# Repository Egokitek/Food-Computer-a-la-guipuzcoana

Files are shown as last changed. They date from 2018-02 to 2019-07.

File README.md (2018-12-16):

# Food-Computer-a-la-guipuzcoana

## Cultivo de alimentos frescos en espacios reducidos mediante un Food Computer

**Proyecto de crowdfunding con** el apoyo de la **Fundación Goteo**, la **Diputación Foral de Gipuzkoa** y [**48 Patrocinadores**](Cofinanciadores.md). La campaña de captación de fondos comenzó el 14 de Septiembre de 2017 y finalizó el 2 de Diciembre del mismo año, habiendo cumplido el objetivo de financiación. EL proyecto se desarrollará durante el año 2018.

 ## Características principales:

**El Food Computer** es la solución ideal para el **cultivo en espacios reducidos en zonas urbanas**, aprovechando cualquier rincón. Es un proyecto de **hardware abierto**, un mini-invernadero con un control muy intenso de las condiciones de cultivo de tal forma que se puede garantizar el clima adecuado. Se pueden cultivar alimentos frescos de km 0. Durante todo el año, fácilmente y con unas tasas de crecimiento muy altas.

**El sistema es escalable**, de tal forma que Food computer tiene 1m3 pero se pueden hacer equipos mas grandes. El consumo de energía es bajo y es posible obtenerlo por vía renovable. Y todo ello con información abierta y disponible para todas en Internet.

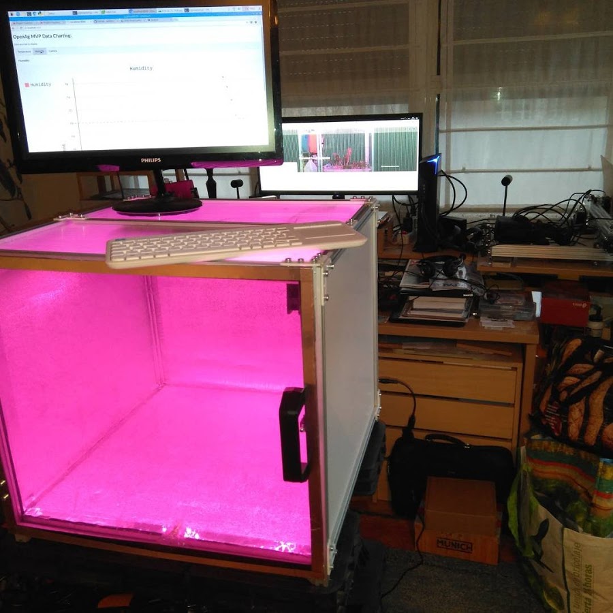
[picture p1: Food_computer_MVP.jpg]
Food Computer MVP


De ese modo se puede cultivar incluso en tierras contaminadas radiactivamente, de hecho el concepto surgió tras una visita a Fukushima de profesorado del MIT. El concepto Food Computer permite conectar vía Internet a otros equipos similares en el mundo, es una especie de red social de agricultores que podrán compartir los parámetros de cultivo o **recetas climáticas** y así conseguir mejorar las cosechas de forma cooperativa y distribuida.

Le quiero añadir funcionalidades que permitan el empleo de biofertilizantes y microorganismos, extracto de agua de mar, etc. Son nutrientes que se pueden crear de forma local y a bajo coste para sustituir a los nutrientes sintéticos que se usan habitualmente en cultivo hidropónico sin tierra. De este modo tendremos un "sustrato vivo" similar al de las tierras mas fértiles y de forma muy asequible y limpia. Integraré también el cultivo de alga spirulina (con una tasa muy elevada de proteínas, calificada de "superalimento").

## Objetivos y recompensas:

Como parte de las recompensas se incluye una unidad de bajo coste y de funciones básicas para comenzar a experimentar, pero el objetivo es construir una unidad completa con todas las funciones y añadir todo lo que se ha comentado. Con ese objetivo cumplido la idea es construir una unidad mas grande de unos 2x2x1m que multiplica las posibilidades. Todo el desarrollo quedará publicado aquí en Github.

## Contenidos de las carpetas:

[**Introducción** ](Introduccion.md) 

Conceptos e Historia del proyecto. Posibilidades que ofrece.

[**Construcción del bastidor** ](Construccion%20bastidor/README.md) 

Varias técnicas constructivas para hacer un bastidor de Food Computer de forma modular, con varios tamaños a elegir.

[**Placa de control - Brain**](Placa%20de%20control%20-%20Brain/README.md) 

Electrónica necesaria para manejar el equipo.

[**Software**](Software/README.md) 

Se utiliza en principio el software **MVP (Minimum Viable Product)**, mas sencillo de implementar y utilizar que el original. 

[**Cultivo**](Cultivo/README.md) 

Metodologías de cultivo.

[**Documentos** ](DOCs/README.md) 

Documentos en formato PDF sobre cultivos de diverso tipo, incluyendo el hidropónico.

[**STLs** ](STL/README.md) 

Ficheros STL listos para imprimir. Necesarios para el desarrollo del proyecto.

[**Varios**](Varios/README.md) 

Diferentes cuestiones que no encajan en el resto de apartados.

## Lista de componentes y presupuesto

El **BOM (Bill of Materials)** está en formato de hoja de calculo excel y tiene varias pestañas que incluye los distintos bastidores realizados y sus diferencias de precio.

En este momento solo está completada la pestaña del FC MVP de 50x50x50 con TSLOT. Próximamente se completará el resto.

El fichero lo tienes [aquí](BOM.xlsx):

## Autor

[**Victor Barahona**](https://github.com/Egokitek)

[**www.egokitek.com**](http://www.egokitek.com)

## Cofinanciadores

[Ver listado **aquí:**](Cofinanciadores.md)

## Créditos

**Food Computer** es un concepto creado por **Caleb Harper** en el **[MIT](http://web.mit.edu/)**, departamento de agricultura abierta **[OpenAg](https://www-prod.media.mit.edu/groups/open-agriculture-openag/overview/)**.

Gran parte de este proyecto está basado en el concepto **[Food Computer MVP](https://forum.openag.media.mit.edu/t/300-food-computer/2343)** (minimum viable product), desarrollado por los miembros de la comunidad OpenAg:
- Peter Webb
- Howard Webb
- Drew Thomas

## Licencia

**GPL3.0**

## En desarrollo actual

- Experimentar y documentar las distintas técnicas de cultivo ya en uso.
- Verificar consumos eléctricos y ver la posibilidad de optimizarlos.
- Probar extracto de agua de mar, biofertilizantes, microorganismos y otros aportes nutricionales.

## Desarrollo futuro

- Integración de cultivo de alga **spirulina**.
- Integración de módulo de **vermicompostaje**.
- Integración de módulo de **acuaponía**.
- Posibilidad de escalado del sistema.

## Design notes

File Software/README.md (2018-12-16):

# Software

### Version MVP

Es la que se ha desarrollado en este proyecto y es la que está utilizando la mayoría de la comunidad. **Ha sido desarrollada por Howard & Peter Webb y Drew Thomas.**

Emplea solo un Raspberry Pi3 sin Arduino, con una tarjeta de 4 relés. Corre sobre un sistema **Linux Raspbian (versión Jessie o Strech)**, a la que se ha añadido los scripts en Python que manejan el equipo.

Desde **Crontab** se controlan las tareas de captura de imágenes, encendido y apagado de luces etc. El sistema contiene un software llamado **Couchdb** que permite almacenar los datos capturados y mantenerlos formateados para verse desde un navegador web.

Desde el navegador **Chromium** (equivalente al Chrome) podemos acceder a los datos mediante un interfaz gráfico. En la foto que sigue vemos su aspecto:

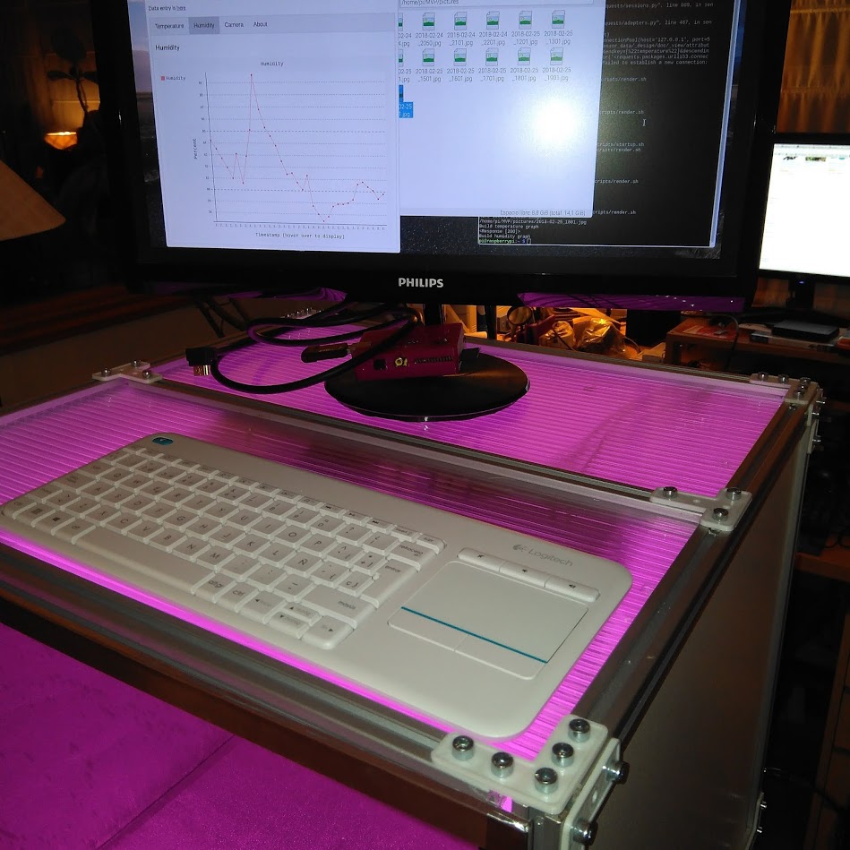
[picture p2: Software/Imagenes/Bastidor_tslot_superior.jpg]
Interfaz gráfico


Tenemos a la izquierda el navegador con la gráfica de humedad seleccionada. A la derecha una carpeta con una serie de fotos capturadas en timelapse del interior.

**Para facilitar la instalación del software**, desde la comunidad se preparó una imagen de la instalación, si se quema directamente a una SD tendremos el software ya instalado y solo tendremos que modificarlo a nivel de variables de entorno. Como esta imagen pesa cerca de 4Gb no se puede incluir aquí.

Para ver el proceso de instalación paso a paso lo veremos mas abajo.

Una vez de tener **una SD configurada podemos clonarla** mediante una aplicación que tiene el sistema Jessie o Strech, de ese modo ahorraremos bastante tiempo en el proceso. Tal y como vemos en esta foto:

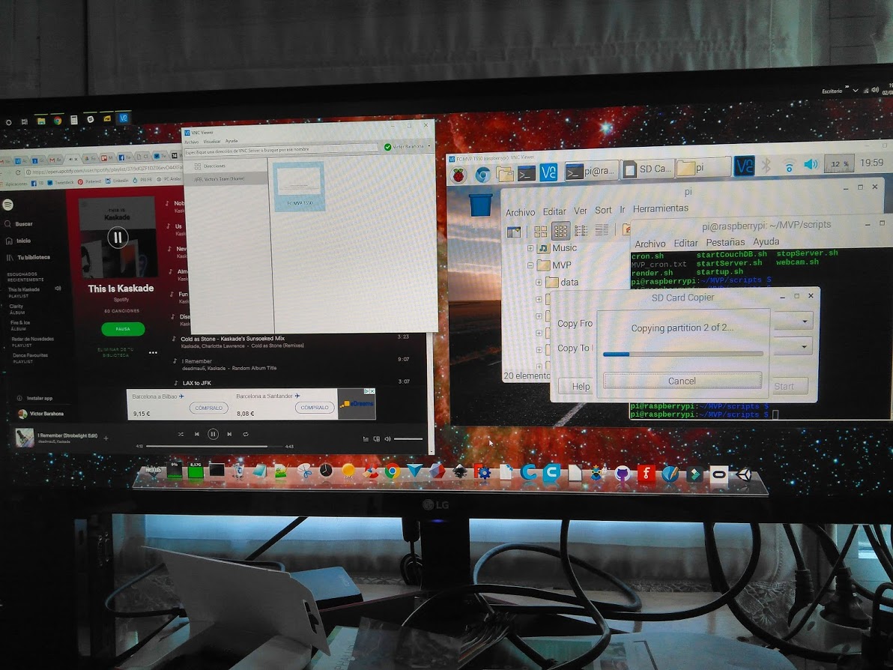
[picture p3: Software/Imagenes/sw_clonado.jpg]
Clonado de software


Una vez de instalado el equipo podemos manejarlo mediante teclado y monitor localmente, o bien habilitar en el Raspberry el **VNC Server** (un SW que lleva incluido por defecto) y **de esa manera podemos operar sobre el de forma remota** desde cualquier lugar. Tal y como vemos aquí:

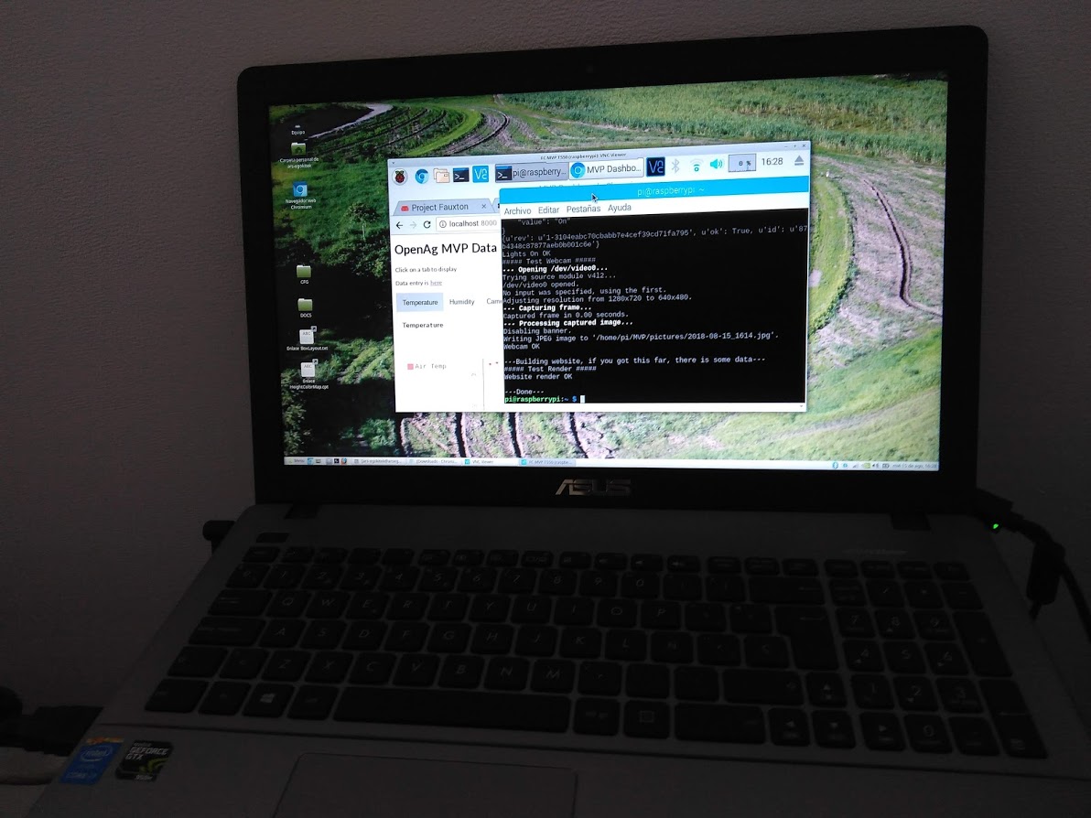
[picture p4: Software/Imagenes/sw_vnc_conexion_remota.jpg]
VNC


Desde el equipo remoto debemos usar el  software VNC viewer. Para ello debemos abrir una cuenta gratuita que nos permitira conectar desde 3 equipos diferentes a 5 unidades. Yo uso mi móvil, el ordenador que tengo en el taller y el ordenador que tengo en la oficina de mi casa. Y puedo conectar a 5 MVPs. Para mas conexiones ya entramos en el plan de pago. Existen alternativas que estoy estudiando.

La comunidad está trabajando también en algún tipo de UI (Interfaz de usuario) que permite operar en varios equipos de forma remota. Se están valorando aplicaciones IoT como NodeRed, Blynk etc. En mi caso sigo utilizando VNC pero si hago algun avance interesante lo publicaré aquí.

### Instalación paso a paso del software

[**En inglés**](Instalation_FC_MVP_ENG.md) Versión original desarrollada por **Howard Webb**

[**En español**](Instalacion_FC_MVP_ESP.md) Versión traducida al castellano  por **Victor Barahona**

La versión en español incluirá modificaciones para utilizar un tercer relé de bombeo de agua y nutrientes. Está en desarrollo y pruebas.

### Comentarios sobre las versiones V1 y V2 del FC

**Las versiones originales del FC V1 y V2** usaban un **Raspberry Pi3, un Arduino y una placa de hasta 16 relés** para controlar los actuadores. Además del software de Arduino la placa Raspberry llevaba su propio software con scripts en JSON y Python. 

Algunos de los problemas que han llevado al abandono de esta línea de trabajo en MArzo de 2018 es la interconectividad de todo este software, problemas con las lecturas de sensores que tenían diferentes tipos de conectores y tensiones de trabajo.

También se comprobaron problemas con la estabilidad del Raspberry Pi debido a que no tiene propiamente un disco duro sino una tarjeta SD que contiene el sistema. Las sucesivas operaciones de lectura/escritura en la misma provocaban una corrupción de datos. Si esta se producía en algún fichero crítico del sistema éste se quedaba "colgado".

### Comentarios sobre la versión V3 EDU

**La nueva V3 EDU** lanzada en Noviembre de 2018 utiliza el **BeagleBone Black Wireless** , una placa que incluye una memoria interna de 4GB que contiene el sistema y es mucho mas robusta, con un slot para micro SD donde se guardan los datos. No se incluye Arduino.

En esta nueva versión tampoco hay placas de relés estandar sino una placa a medida donde se inserta el Beaglebone. En esa placa están insertos los drivers y circuitería necesaria para operar todo el sistema. Los planos e han liberado en Noviembre de 2018 y todavía se está discutiendo en la comunidad la manera mas económica de poder fabricarla, ya que al ser de 30x30 cm su producción es bastante costosa.

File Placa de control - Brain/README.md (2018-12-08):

# Placa de control - Brain

#### [MVP - Brain ](MVP_Brain.md) 

Placa de control necesaria para manejar el equipo.

#### [Iluminación LED ](Iluminacion_LED.md) 

Testeo de diferentes fórmulas para uso de LEDs en el cultivo.

- Paneles matriciales de diferentes potencias
- Tiras de LED
- LEDs de tipo COB (espectro total)
- Montajes DIY a la medida
- Cuestiones de refrigeración
- PAR, Lumen, Lux, umol ... La cuestión de la eficacia luminosa y como medirla.

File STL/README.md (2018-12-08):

# STLs del proyecto

**En esta carpeta se contienen los ficheros STL necesarios para el desarrollo del proyecto**

Puedes verlos con el visualizador integrado en Github o bien mediante programas como Cura, Repetier etc

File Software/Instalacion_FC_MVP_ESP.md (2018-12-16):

# Instalación del Software MVP III

#### Versión en español(castellano) traducida por Victor Barahona

# MVP III

## Último lanzamiento: 3.1.8

### Registro de cambios: 2018/11/24

 - Arreglar la descarga binaria de CouchDB para modificar la propiedad a couchdb
 - Cambio propiedad de los archivos de registro para solucionar el problema de escritura
 - Agregue un script java a index.html para dar a los gráficos un nombre único (solución al problema de almacenamiento en caché de Chrome)

Registro de cambios: 2018/10/2
 - Se agregó CouchDB binario para solucionar problemas de compilación
 - NOTA: Fuxton no está incluido en este binario.

Registro de cambios: 2018/09/24
 - agregue chmod a Startup.sh para que los registros siempre tengan el permiso de escritura correcto

Registro de cambios: 2018/09/21
  - Corregir error tipográfico en Startup.sh

Registro de cambios: 2018/07/05
  - Importante cambio en la estructura JSON de datos, esta debería ser la versión final.
  - Se eliminó la dependencia SI7021 de smbus, reemplazado con python-periferia
  - Se agregó StartUp.py para verificar el estado de las luces al reiniciar
  - Se agregó HeartBeat.py para comprobar que CouchDB está en funcionamiento o se reiniciará automáticamente para reiniciar el sistema.
  - Eliminado el acceso web a CouchDB
  - Cambios de nombre de archivo y método para mantener la coherencia con el estándar de código de Python
  - Añadir registro estándar de Python
  - Se eliminó la recuperación de información geo debido a la desaprobación de la API

## Introducción

Contiene el código e instrucciones necesarias para construir el 'cerebro' del Food Computer MVP. Es principalmente una colección de código en Python que se ejecuta en un Raspberry Pi. Vea los [**foros OpenAg**](http://forum.openag.media.mit.edu/) para obtener información sobre los distinots temas involucrados.

El MVP (producto mínimo viable) es una versión simplificada del Food Computer desarrollado por OpenAg MIT.

## Antes de empezar

 - Sigue las instrucciones para construir un sistema Raspbian (Noobs).
 - Configurar el entorno (ver más abajo). Activa VNC, esta es la forma más fácil de ver múltiples Raspberry Pis sin necesidad de teclados y monitores separados para cada uno. Puedes ver todas los MVPs en tu red local a través de un solo Raspberry, o descargar VNC en un PC y acceder a ellos a través de un PC.

## Construyendo múltiples MVPs

Una vez que has configurado una tarjeta SD, desde el menú principal, use la aplicación de copia de tarjeta SD para replicar el sistema para los otros MVP. Solo asegúrate de ejecutar lo siguiente para que se cree una ID única para cada MVP.
  
  > python /home/pi/MVP/python/Environment.py

## Arquitectura:

El cerebro de MVP se compone en su mayoría de scripts de Python que utilizan cron como el programador horario. Python y cron están integrados en el sistema operativo Raspbian, y la biblioteca Raspberry para manipular los pines GPIO ya está cargada.

El Python es modular, por lo que las adiciones y los cambios se pueden hacer fácilmente sin afectar a todo el sistema.

- Control de programación (cron)
  - Captura de imágenes (webcam.sh)
  - Sensores de registro (LogSensors.py)
  - Encender las luces (LightOn.py)
  - Apagar las luces (LightOff.py)
  - Comprobar la temperatura (termostato.py)
  - Actualizar gráficos e imágenes para la interfaz de usuario (Render.sh)

CouchDB es el principal sistema de almacenamiento de datos y proporcionará una fácil replicación en la nube en el futuro.

Para obtener más información sobre Cron [ver aquí:](https://docs.oracle.com/cd/E23824_01/html/821-1451/sysrescron-24589.html)

## Descripción del hardware:

**Ventilador:**
Hay dos ventiladores, uno para circulación y otro para eliminar el exceso de calor. Estos funcionan con una fuente de 12V, el primero va conectado directamente y el segundo pasará a través de la tarjeta de relés.

**Sensor de temperatura / humedad:**
El sensor SI7021 usa el bus I2C para medir la temperatura y la humedad. Mas información en [Instrucciones](https://learn.adafruit.com/adafruit-si7021-temperature-plus-humidity-sensor/overview) para saber sobre su uso y el cableado.

**Cámara web:**
Se usa una cámara USB estándar para obtener imágenes (aunque la cámara Raspberry Pi es una opción). Consulte [aquí](https://www.raspberrypi.org/documentation/usage/webcams/) para obtener instrucciones.

**Tarjeta de Relés:**
Se utiliza un conjunto de relés controlados por los pines GPIO para encender y apagar las luces (220 V) y el ventilador de extracción (12 V). Suele ser una tarjeta de 4 relés. El diseño estandar del MVP emepla solo 2, los otros dos son de repuesto. En mi caso emplearé un tercero para bombeo de agua y nutrientes, está en fase de desarrollo y pronto quedaré implementado aquí.

## Asignación de Pines:

Consulta el siguiente [diagrama](https://docs.particle.io/datasheets/raspberrypi-datasheet/#pin-out-diagram) para ver la asignación de pines del Raspberry:

El código se ha desarrollado de acuerdo a la convención indicada arriba.

- 3  SDA a SI7021
- 5  SCL a SI7021
- 29 relé de luz (relé # 4)
- 31 (reservado para el relé # 3)
- 33 (reservado para el relé # 2)
- 35 Control de ventilador GPIO13 (relé # 1)

## Instalación

### Asegurarse de tener lo siguiente:

1. Instalación NOOB de Raspbian en Raspberry Pi
2. El sistema Raspbian ha sido configurado (mediante **raspi-config**)
    - para localización (hora, zona horaria)
    - El wifi está establecido y conectado.
    - I2C ha sido habilitado
    - VNC está habilitado para un acceso remoto
    - La resolución de la pantalla está configurada en Modo 16 para una correcta visualización de VNC
    
2. Tarjeta SD 32G para guardar datos
3. Los sensores y el relé están conectados al Pi. Si intentas ejecutar el código sin sensores, se producirá un error (error de E / S, en la función **get_tempC ()**). Esto se trasladará hasta el error de la tarea cron para **LogSensor.py**.

### Pasos a seguir:

Los scripts de construcción forman parte de la documentación. Si quieres construir cosas por ti mismo, sigue y/o modifica los scripts (/ home / pi / MVP / setup).

**El script de instalación principal** no se encuentra en Github, ya que  extrae los archivos de Github y cambia los permisos en **/home/pi/MVP/setup/releaseScript.sh** . Para crearlo debes seguir los siguientes pasos:

- Desde tu Raspberry Pi, corta y pega las siguientes líneas de código en un archivo de texto y asígnale el nombre **buildScript.sh** . 
- Luego, cambia los permisos para hacerlo ejecutable (desde un Administrador de archivos, haz clic derecho en el archivo y selecciona "Propiedades". 
- En la pestaña "Permisos", debajo de "Ejecutar", selecciona "Cualquiera" y luego haz clic en "Aceptar"). 
- Luego abre una ventana de shell-terminal y escribe **ruta de acceso a su archivo/buildScript.sh** .

**A continuación el texto del script que debes copiar/pegar:**

```
#!/bin/sh

# Part 1
# Semi-generic script to get and install github archive
# Author: Howard Webb
# Date: 10/02/2018

# This script assumes you are running on your Raspberry Pi with (Stretch) Raspbian installed.
# Internet is connected
# You have configured the local environment (keyboard, timezone)
# You have adjusted the Pi Preferences (Configuration)
#   Enable the camera interface
#   Enable I2C
#   Enable VNC
#   Set screen resolution to Mode 16
#   Optionally (suggested) enable SSH, VCN and 1-Wire

# Get the release from Github
# Extract it to the proper directory
# Make the build script executable
# Run the release specific build script

###### Declarations #######################

RED='\033[31;47m'   # Define red text
NC='\033[0m'        # Define default text

EXTRACT=/home/pi/unpack    # Working directory for download and unzipping
TARGET=/home/pi/MVP       # Location for MVP
RELEASE=mvp             # Package (repository) to download 
VERSION=v3.1.8         # github version to work with
ZIP_DIR=3.1.8
GITHUB=https://github.com/futureag/$RELEASE/archive/$VERSION.zip    # Address of Github archive

echo $EXTRACT
echo $TARGET
echo $RELEASE
echo $GITHUB

###### Error handling function ###################

PROGNAME=$(basename $0)

error_exit()
{
	echo ${RED} $(date +"%D %T") "${PROGNAME}: ${1:="Unknown Error"}" ${NC} 1>&2
	tput sgr0
	exit 1
}

####### Start Build ######################
echo "##### Update Existing System #####"
sudo apt-get update

echo "##### Starting to build directories #####"
# Build target directory
mkdir -p $TARGET || error_exit "Failure to build target directory"
echo $(date +"%D %T") $TARGET" built"

echo "##### Starting download of MVP from Github #####"
# Download MVP from GitHub and install
# Build extraction directory
mkdir -p $EXTRACT || error_exit "Failure to build working directory"
echo $(date +"%D %T") "Directory built"
cd $EXTRACT

# Download from Github
wget -N $GITHUB -O $VERSION.zip || error_exit "Failure to download zip file"
echo $(date +"%D %T") "MVP Github downloaded"

cd $EXTRACT

# Unzip the files, overwrite older existing files without prompting
unzip -uo $EXTRACT/$VERSION.zip || error_exit "Failure unzipping file"
echo $(date +"%D %T") "MVP unzipped"

cd $EXTRACT/$RELEASE-$ZIP_DIR/MVP || error_exit "Failure moving to "$EXTRACT/$RELEASE"-"$ZIP_DIR

# Move to proper directory
mv * $TARGET
echo $(date +"%D %T") "MVP moved"

########################################
echo "##### Relsease Specific Build #####"
# Complete the release specific build - this is the CouchDB extract

# Set permissions on script
chmod +x $TARGET/setup/releaseScript.sh || error_exit "Failure setting permissions on release script (check file exists in MVP/scripts)"
echo $(date +"%D %T") "Run permissions set"

# Run script in download
bash $TARGET/setup/releaseScript.sh || error_exit "Failure running release specific script"

# Clean up temporary extraction directory
rm -r $EXTRACT
echo $(date +"%D %T") $EXTRACT" removed"

echo $(date +"%D %T") "Install Complete"

```

## Instalación paso a paso

Los siguientes scripts (en / home / pi / MVP / scripts) pueden ejecutarse por separado y en secuencia si se encuentran errores. Busca dentro de los scripts para comandos individuales.

- **releaseScript.sh** llama a los siguientes scripts:
- **releaseScript_DB.sh** instala el código CouchDB.
- **releaseScript_Local.sh** construye bibliotecas, inicia la base de datos e inicializa procesos.
- **releaseScript_Test.sh** llama a **Validate.sh** para probar el sistema
- **releaseScript_Final.sh** configura el inicio y carga cron

## Desarrollo futuro (con prioridad):

- Agregar un **watchdog** perro guardián al Raspberry.
- Corregir las notificaciones de correo electrónico cron.

## Desarrollo futuro (sin prioridad):

- Interfaz GUI para configurar variables persistentes (podría ser local)
- Agregar una bomba para cuando tenga que estar ausente por un tiempo y se tenga que rellenar el depósito.
- Control de luz para LEDs controlables.

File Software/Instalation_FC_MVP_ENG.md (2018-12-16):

# Instalation of Software: MVP III

#### English versión developed by Howard Webb

# MVP III

## Latest Release: 3.1.8

### Change Log: 2018/11/24

 - Fix CouchDB binary download to modify ownership to couchdb
 - Chanage ownership of log files to fix write problem
 - Add java script to index.html to give charts a unique name (Chrome caching problem fix)

Change Log: 2018/10/2
 - Added binary CouchDB to get around build problems
 - NOTE: Fuxton is not included in this binary

Change Log: 2018/09/24
 - add chmod to Startup.sh so logs always have the correct write permission

Change Log: 2018/09/21
  - Correct typo in Startup.sh

Change Log: 2018/07/05
  - Major change to the data JSON structure, this should be the final version
  - Removed SI7021 dependency on smbus, replaced with python-periphery
  - Added StartUp.py to check state of lights when reboot
  - Added HeartBeat.py to check CouchDB is up and running, or else will reboot automatically to reset the system
  - Removed web access to CouchDB
  - File and method name changes for consistency with the python code standard
  - Add standard Python logging
  - Removed retreival of geo information due to API deprecation

## Background 

Code and instructions for building the 'brain' of the controled environment hydroponics unit. It is mostly a collection of python code that runs on a Raspberry Pi (or similar device).  See the OpenAg [forums](http://forum.openag.media.mit.edu/) for discussion and issues:

The MVP (Minimal Viable Product) is a simplified version of the MIT OpenAg Food Computer.

## Assumptions

 - Follows the instructions for building a Raspbian (Noobs) system.
 - Configure the environment (see below).  Turn VNC on, this is the easiest way to view multiple Raspberry Pis without needing separate keyboards and monitors for each.  You can view all the Raspberries on your local network through one Raspberry, or download VNC to a PC and access them through a PC.
 
## Building multiple MVPs

Once you have configured one SD card, from the main menu, use the Accessories/SD Card Copier to replicate the system for the other MVPs.  Just be sure to run the following so that a unique ID will be created for each MVP.
  
  > python /home/pi/MVP/python/Environment.py

## Architecture:

The MVP brain is mostly python scripts involed using cron as the scheduler.  
Python and cron are built into the Raspbian OS, and the Raspberry library to manipulate GPIO pins is already loaded.

The Python is modular so additions and changes can easily be made without affecting the whole system.

- Scheduling Control (cron)
  - Image capture (Webcam.sh)
  - Log Sensors (LogSensors.py)
  - Turn lights On (LightOn.py)
  - Tirm lights Off (LightOff.py)
  - Check Temperature (Thermostat.py)
  - Refresh charts and picture for the UI (Render.sh)

CouchDB is the main data storage system, and will provide easy replication to the cloud in the future.

For more information on Cron [see:](https://docs.oracle.com/cd/E23824_01/html/821-1451/sysrescron-24589.html)

## Hardware Build:

**Fan:**
There are two fans, one for circulation and one for exhausting excess heat  These can run off the Raspberry's 5V or from a external 12V transformer

**Temperature/Humidity Sensor:**
A SI7021 sensor on an I2C bus is used for temperature and humidity.  See the following for (instructions)[https://learn.adafruit.com/adafruit-si7021-temperature-plus-humidity-sensor/overview] on use and wiring.

**Webcam:**
A standard USB camera is used for imaging (though the Raspberry Pi camera is an option).  See [here](https://www.raspberrypi.org/documentation/usage/webcams/) for instructions

**Relay:**
A set of relays controled by GPIO pins is used to turn lights on and off (120V), and the exhaust fan (12V)

# Pin Assignment:

Refer to the following [diagram](https://docs.particle.io/datasheets/raspberrypi-datasheet/#pin-out-diagram) for the Raspberry's pin names:

Code follows the board number convention.

- '3 - SDA to SI7021'
- '5 - SCL to SI7021'
- '29 - light relay (relay #4)'
- '31 - (reserved for relay #3)'
- '33 - (reserved for relay #2)'
- '35 - GPIO13 fan control (relay #1)'

## Build Activities

### Assumptions:

1. NOOB install of Raspbian on Raspberry Pi
2. The Raspbian system has been configured 
    - for localization (time, timezone)
    - wifi is established and connected
    - I2C has been enabled
    - VNC is enabled for easy remote access
    - Screen resolution is set to Mode 16 for proper VNC viewing
    
2. 32G SD card to hold data
3. Sensors and relay are wired to the Pi.  If you try to run the code without sensors, some of it will error out (I/O Error, I noticed in the get_tempC() function).  This will ripple up to error out the cron job for LogSensor.py.

### Software Build

The build scripts are the documentation.  If you want to build things yourself, follow the scripts (/home/pi/MVP/setup).
The initial script is not in Github, as the script extracts the files from Github and changes the permissions on /home/pi/MVP/setup/releaseScript.sh.  From within your Raspberry Pi, cut and paste the following lines of code to to a text file and name is buildScript.sh.  Then change, the permissions to make it executable (from a File Manager, right click on the file and select "Properties".  In the "Permissions" tab, under "Execute", select "Anyone" and then click "OK").  Then open a terminal window and type in "<path to your file>/buildScript.sh.   

```
#!/bin/sh

# Part 1
# Semi-generic script to get and install github archive
# Author: Howard Webb
# Date: 10/02/2018

# This script assumes you are running on your Raspberry Pi with (Stretch) Raspbian installed.
# Internet is connected
# You have configured the local environment (keyboard, timezone)
# You have adjusted the Pi Preferences (Configuration)
#   Enable the camera interface
#   Enable I2C
#   Enable VNC
#   Set screen resolution to Mode 16
#   Optionally (suggested) enable SSH, VCN and 1-Wire

# Get the release from Github
# Extract it to the proper directory
# Make the build script executable
# Run the release specific build script

###### Declarations #######################

RED='\033[31;47m'   # Define red text
NC='\033[0m'        # Define default text

EXTRACT=/home/pi/unpack    # Working directory for download and unzipping
TARGET=/home/pi/MVP       # Location for MVP
RELEASE=mvp             # Package (repository) to download 
VERSION=v3.1.8         # github version to work with
ZIP_DIR=3.1.8
GITHUB=https://github.com/futureag/$RELEASE/archive/$VERSION.zip    # Address of Github archive

echo $EXTRACT
echo $TARGET
echo $RELEASE
echo $GITHUB

###### Error handling function ###################

PROGNAME=$(basename $0)

error_exit()
{
	echo ${RED} $(date +"%D %T") "${PROGNAME}: ${1:="Unknown Error"}" ${NC} 1>&2
	tput sgr0
	exit 1
}

####### Start Build ######################
echo "##### Update Existing System #####"
sudo apt-get update

echo "##### Starting to build directories #####"
# Build target directory
mkdir -p $TARGET || error_exit "Failure to build target directory"
echo $(date +"%D %T") $TARGET" built"

echo "##### Starting download of MVP from Github #####"
# Download MVP from GitHub and install
# Build extraction directory
mkdir -p $EXTRACT || error_exit "Failure to build working directory"
echo $(date +"%D %T") "Directory built"
cd $EXTRACT

# Download from Github
wget -N $GITHUB -O $VERSION.zip || error_exit "Failure to download zip file"
echo $(date +"%D %T") "MVP Github downloaded"

cd $EXTRACT

# Unzip the files, overwrite older existing files without prompting
unzip -uo $EXTRACT/$VERSION.zip || error_exit "Failure unzipping file"
echo $(date +"%D %T") "MVP unzipped"

cd $EXTRACT/$RELEASE-$ZIP_DIR/MVP || error_exit "Failure moving to "$EXTRACT/$RELEASE"-"$ZIP_DIR

# Move to proper directory
mv * $TARGET
echo $(date +"%D %T") "MVP moved"

########################################
echo "##### Relsease Specific Build #####"
# Complete the release specific build - this is the CouchDB extract

# Set permissions on script
chmod +x $TARGET/setup/releaseScript.sh || error_exit "Failure setting permissions on release script (check file exists in MVP/scripts)"
echo $(date +"%D %T") "Run permissions set"

# Run script in download
bash $TARGET/setup/releaseScript.sh || error_exit "Failure running release specific script"

# Clean up temporary extraction directory
rm -r $EXTRACT
echo $(date +"%D %T") $EXTRACT" removed"

echo $(date +"%D %T") "Install Complete"

```

## Manual Build
The following scripts (in /home/pi/MVP/scripts) can be run separately and in sequence if any errors are encountered.  Look within the scripts for single commands.

- releaseScript.sh calls the following scripts:
- releaseScript_DB.sh - installs the CouchDB code
- releaseScript_Local.sh - builds libraries, starts the database and initializes things
- releaseScript_Test.sh - calls Validate.sh to test the system
- releaseScript_Final.sh - configures start-up and loads cron

## To Do:

1. Add a watchdog to the Raspberry
2. Fix the cron email notifications

## Future Development (in no priority):

- GUI interface for setting persistent variables (could be local)
- Add a pump for when have to be away for a while and need to refill the reservoir.
- Light control for controlable LEDs

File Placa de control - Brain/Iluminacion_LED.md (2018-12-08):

# Iluminación LED

**Se han testeado diferentes fórmulas para uso de LEDs en el cultivo.**

- Paneles matriciales de diferentes potencias

- Tiras de LED

- LEDs de tipo COB (espectro total)

- Montajes DIY a la medida

- Cuestiones de refrigeración

- PAR, Lumen, Lux, umol ... La cuestión de la eficacia luminosa y como medirla.

### Panel DIY con modulos COB de 10W a 12 Voltios DC

Esta fórmula es interesante ya que es barata y trabaja a 12V de continua, que permite una utilización directa con instalaciones de energía renovable. La pega es que al hacer las soldaduras de forma manual existe mas posibilidad de averías. Puede llegarse a quemar algún componente y tratándose de equipos que van a funcionar desatendidos durante muchas horas no lo recomiendo en absoluto.

### La seguridad ante todo

Aquí vemos dos LED con dos pequeñas placas que bajan la tension de 12 a 9V para que no se calienten tanto. Todo el conjunto está pegado a una barra de aluminio que actua como disipador y además lleva detrás un ventilador. Aún con todo se calientan mucho. **Para jugar y experimentar está bien pero insisto no recomiendo esta vía.**

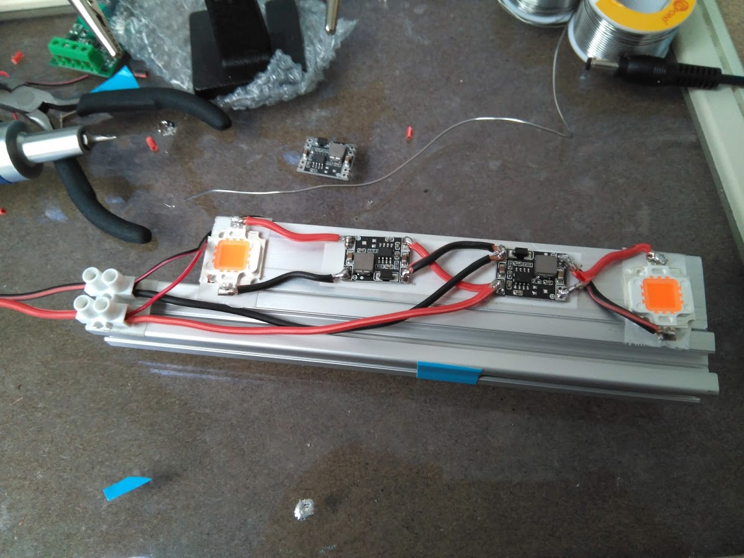
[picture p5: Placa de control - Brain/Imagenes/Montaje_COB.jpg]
Montaje de modulo


Aquí vemos dos COB de luz blanca:

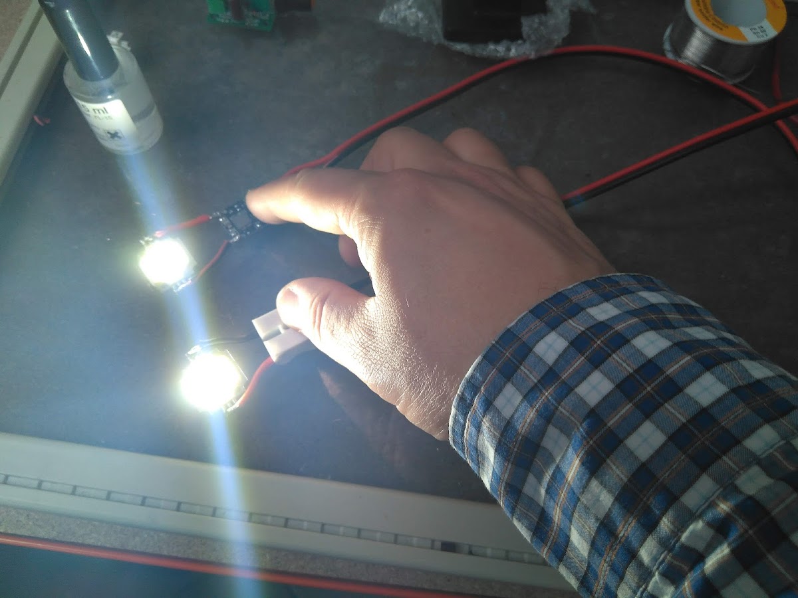
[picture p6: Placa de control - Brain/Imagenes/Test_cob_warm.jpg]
Testeo de COB Warm


Y aquí uno de luz azul-roja que da el color morado:

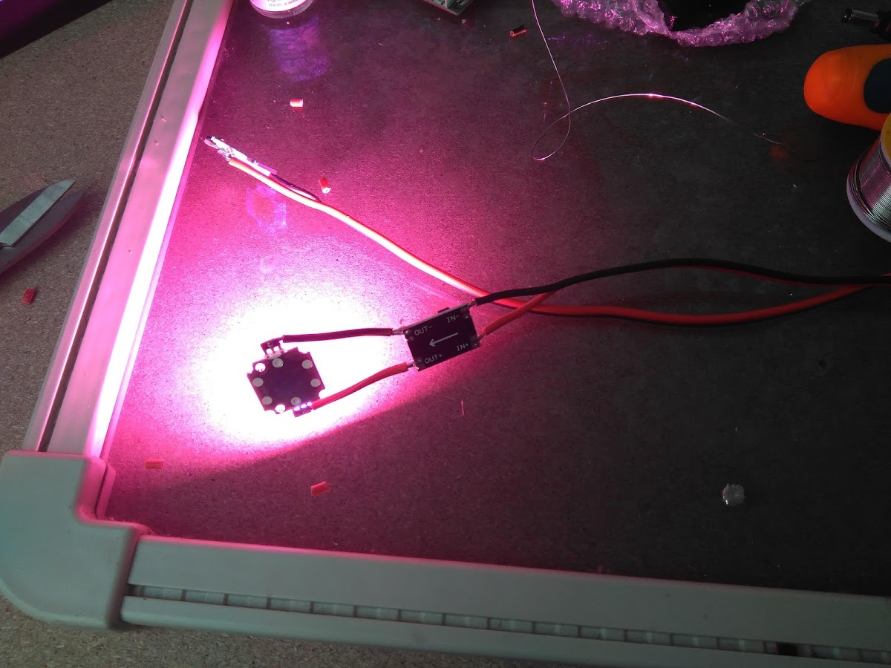
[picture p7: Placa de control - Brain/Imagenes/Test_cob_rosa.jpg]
Testeo de COB rosa


en esta foto podemos apreciar que el conjunto es realmente luminoso:

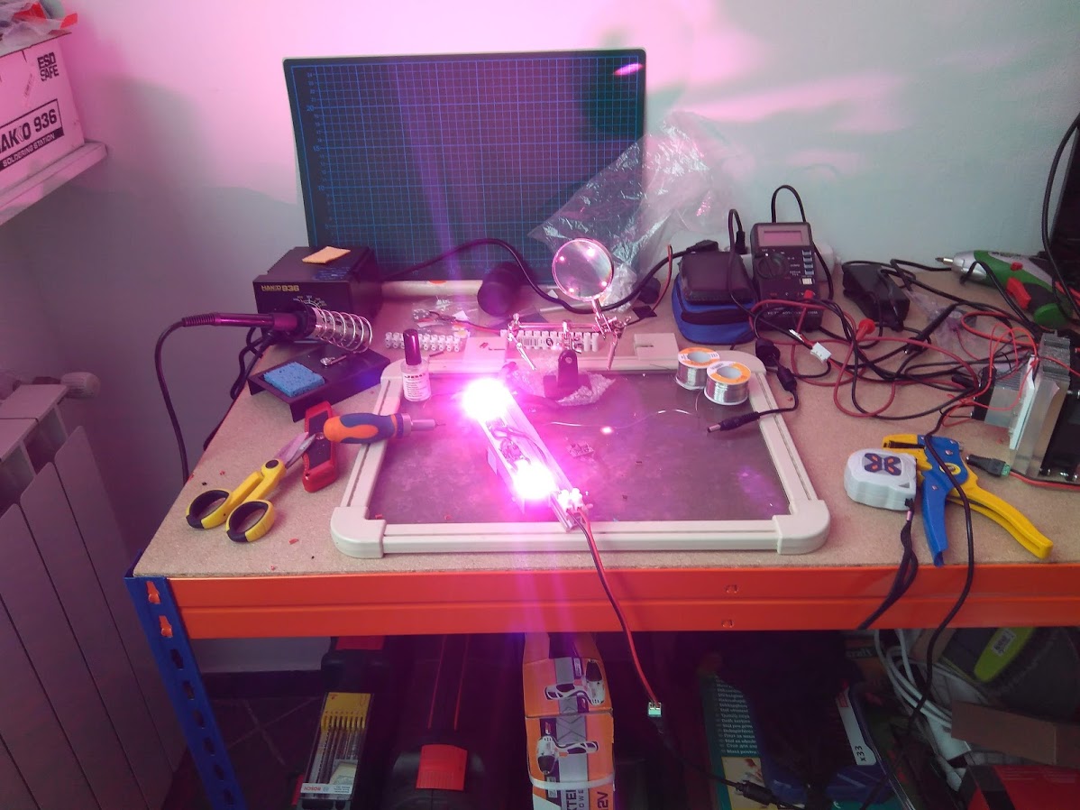
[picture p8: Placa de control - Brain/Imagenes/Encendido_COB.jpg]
Encendido_COB


### Panel comercial de 40W a 220V Voltios AC

Este panel consume tan poco que para disipar el calor le basta con la plancha trasera de aluminio. Trabajan a unos 35V de continua, es lo que ofrece su propia fuente de alimentación.

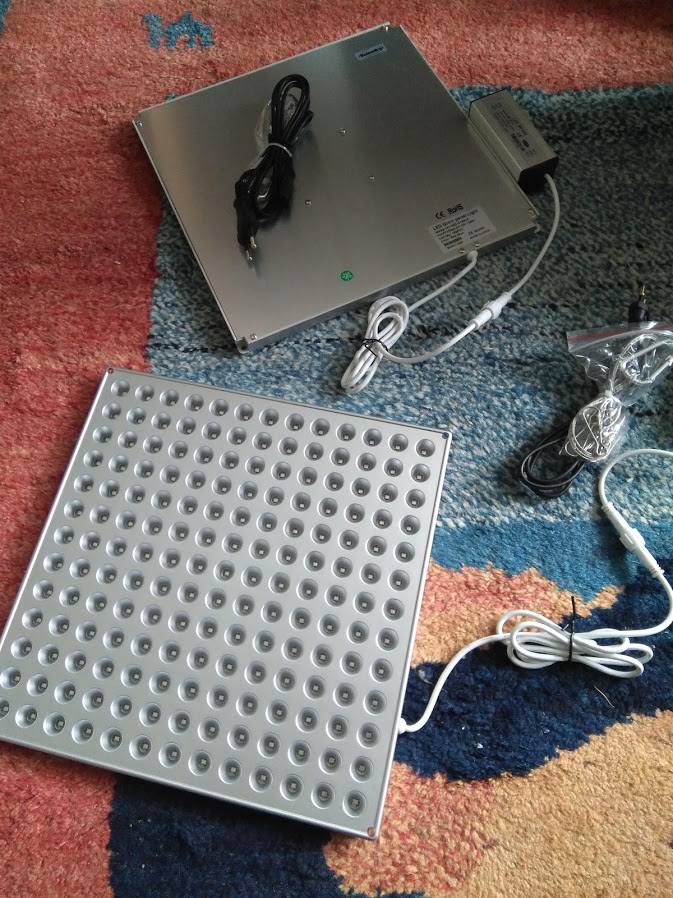
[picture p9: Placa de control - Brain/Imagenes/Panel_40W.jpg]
Panel_40W


Una prueba de endendido:

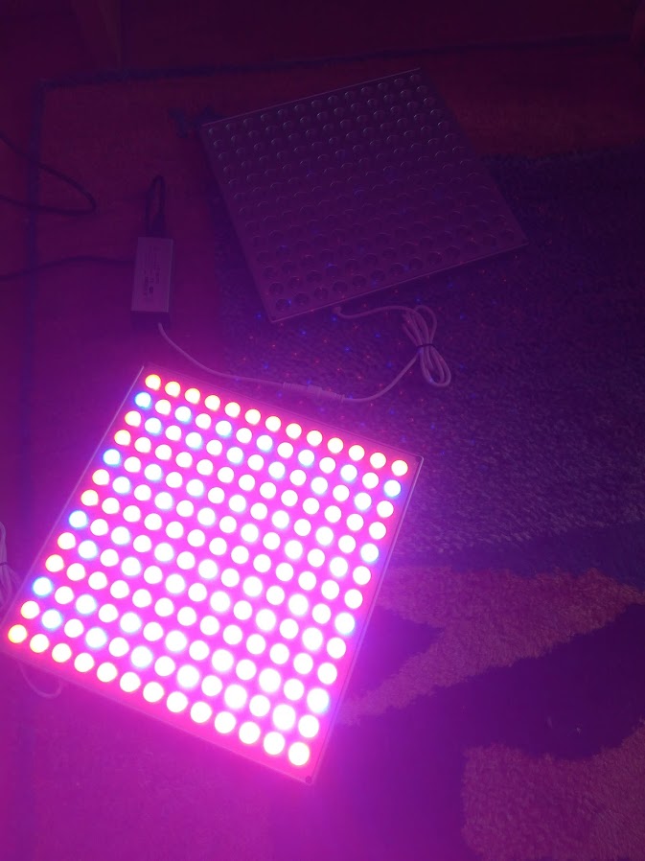
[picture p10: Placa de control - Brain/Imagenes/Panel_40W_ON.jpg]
Panel_40W_ON


En esta foto vemos la combinación de colores, en estas placas es estrictamente rojo-azul. 

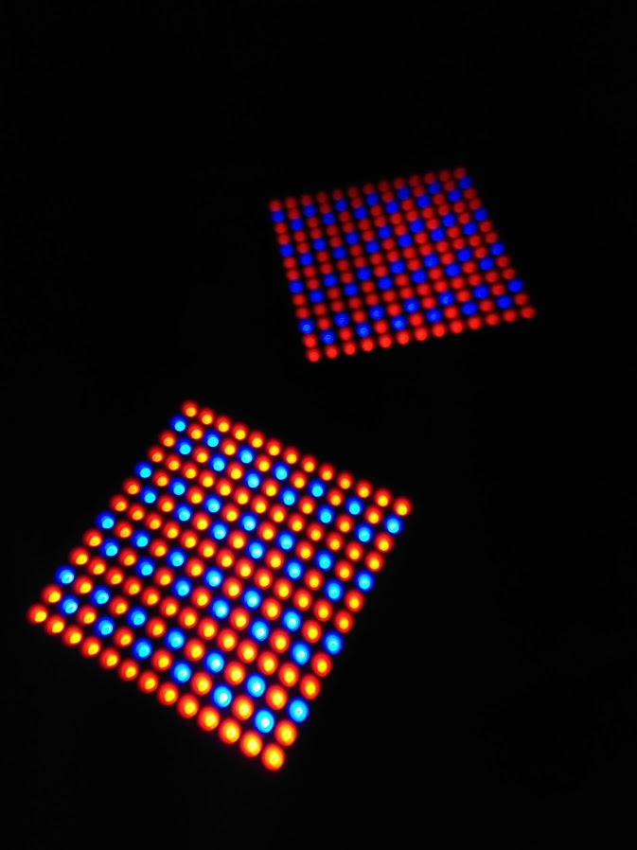
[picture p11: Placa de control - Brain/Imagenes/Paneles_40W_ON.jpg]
Paneles_40W_ON


Hay otras que incluyen algunos LED de infrarojo cercano, blanco etc, para dar una diversidad adicional al espectro luminoso que se emite, como en la de esta foto:

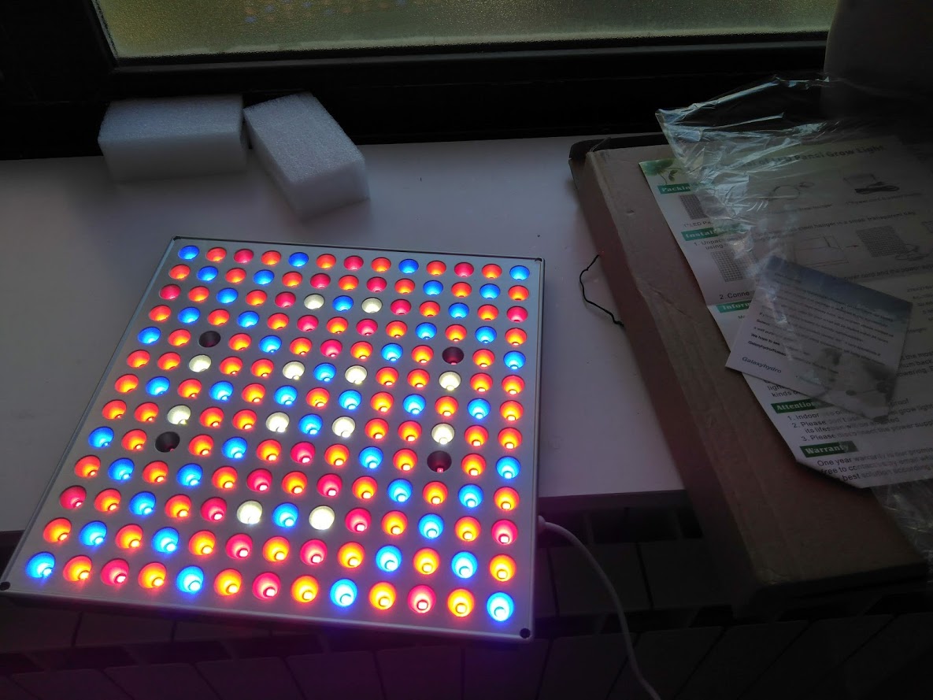
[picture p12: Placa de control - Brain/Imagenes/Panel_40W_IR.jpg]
Paneles_40W_IR


### Panel comercial de 85W a 220V Voltios AC

En este caso tenemos una barra LED, las he visto de varios tamaños: 45, 85 y 110 cm de largo aproximadamente. En nuestro caso utilizo de 85cm. Tiene una altura y un fondo de unos 3cm y no pesan mucho. Se cuelgan del techo mediante hembrillas. Este sistema me ha gustado bastante pero veremos que resultados va dando. Aquí una foto del producto:

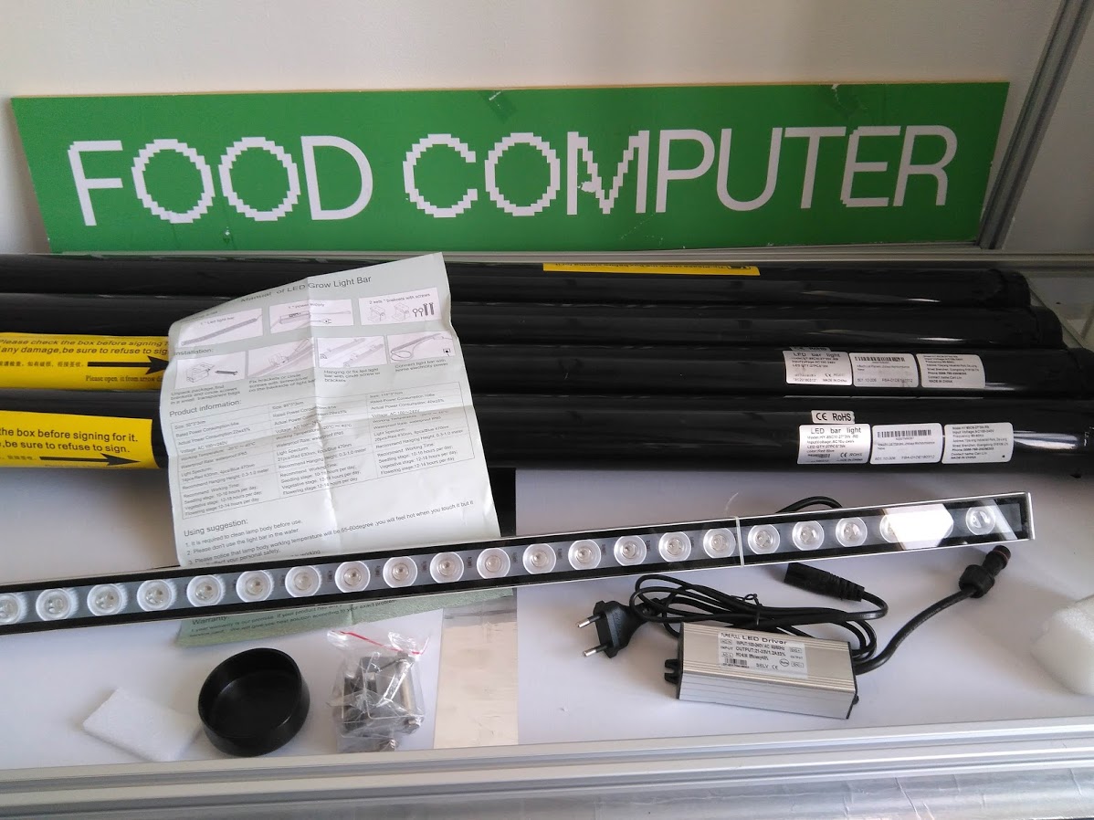
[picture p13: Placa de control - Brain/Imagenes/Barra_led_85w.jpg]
Barra_led_85W


Aquí las vemos instalada sobre hembrillas que previamente hemos fijado al techo del módulo:

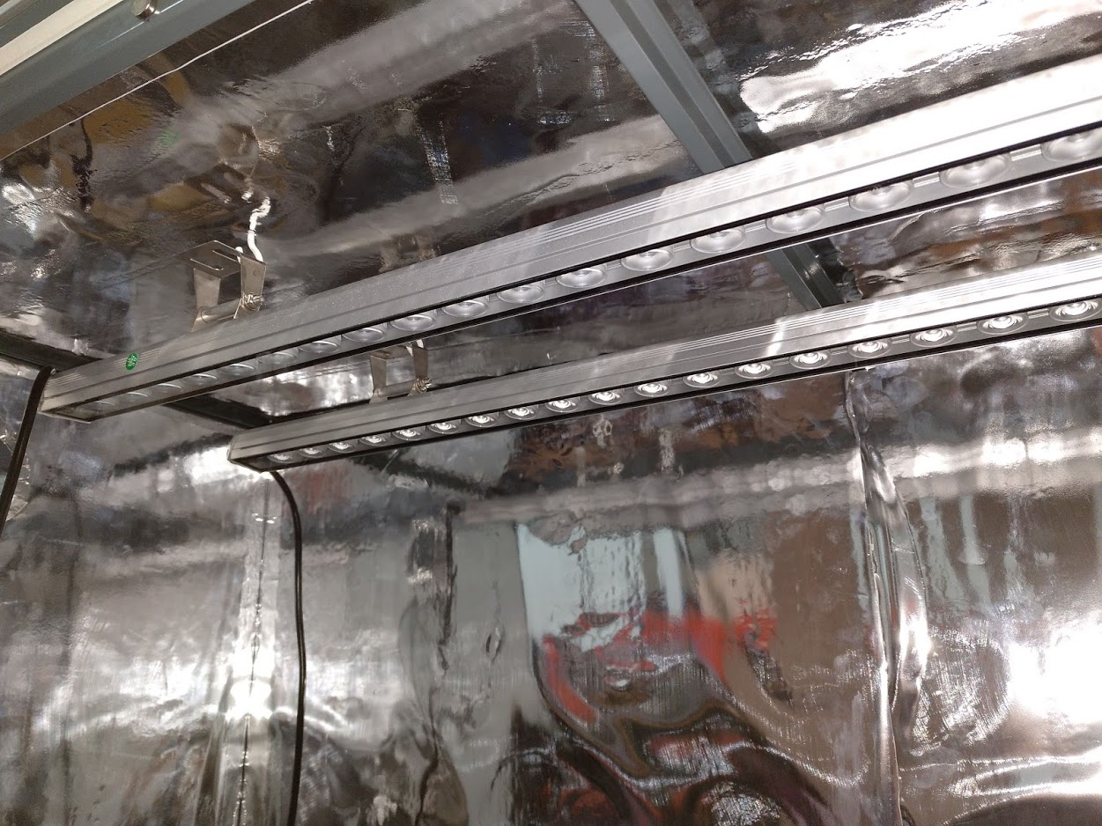
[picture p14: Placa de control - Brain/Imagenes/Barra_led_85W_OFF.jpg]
Barra_led_85W_OFF


Y aquí las vemos encendida:

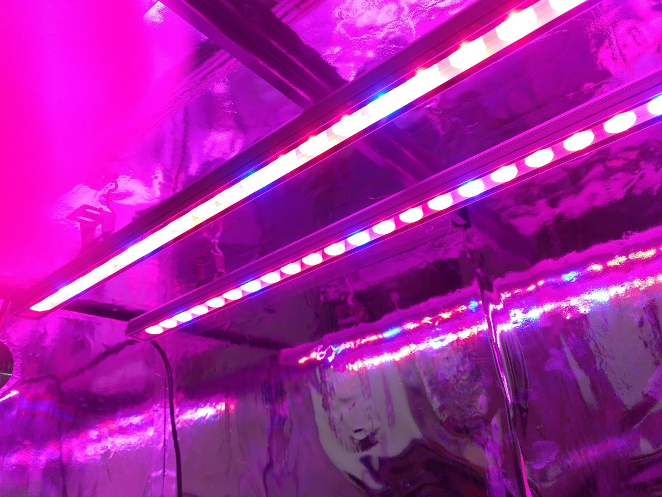
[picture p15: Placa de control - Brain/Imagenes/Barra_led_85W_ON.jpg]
Barra_led_85W_ON


### Panel comercial de 300W a 220V Voltios AC

Este modulo es bastante mas potente y por tanto disipa mas calor. Necesita un buen radiador y ventiladores para disipar este calor. Todo ello está colocado dentro de su caja, lo que hace al conjunto un poco pesado a mi entender. Se pueden unir en **daisy-chain**, es decir, se pueden empalmar varios entre si desde un único enchufe

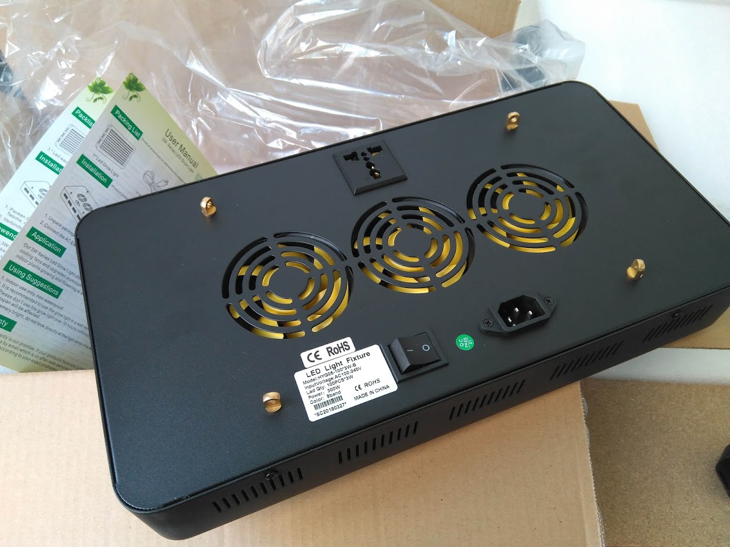
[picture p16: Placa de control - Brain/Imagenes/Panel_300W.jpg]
Panel_300W


Una prueba de encendido:

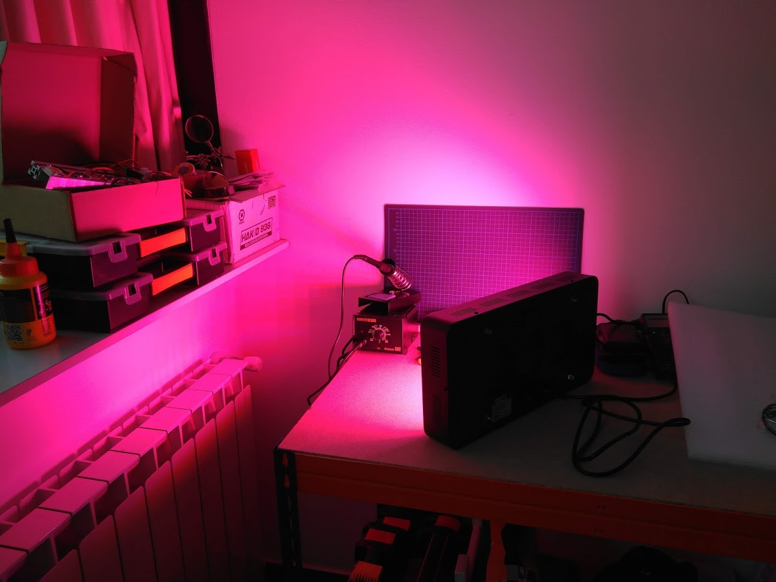
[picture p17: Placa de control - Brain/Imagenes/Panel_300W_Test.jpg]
Panel_300W_Test


Y aquí lo vemos encendido dentro de un Food Computer:

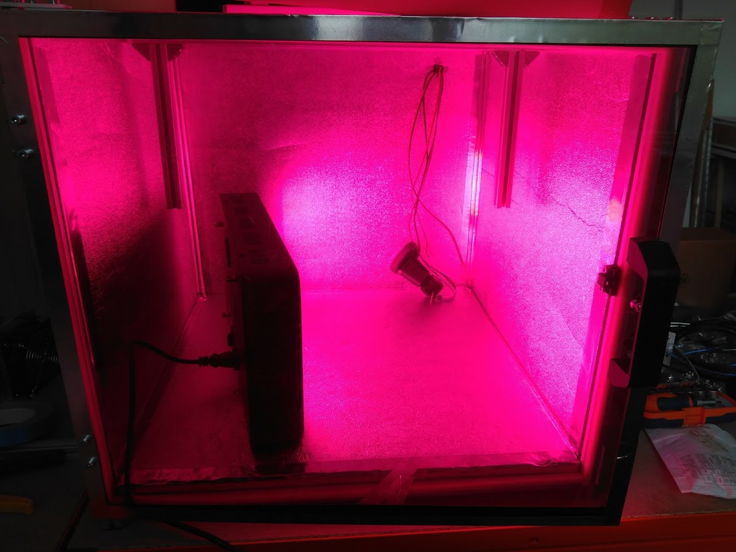
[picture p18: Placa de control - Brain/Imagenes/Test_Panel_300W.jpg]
Test_Panel_300W


Seguiré experimentando con el tema de luces, pero de momento utilizaré las que os he mostrado.

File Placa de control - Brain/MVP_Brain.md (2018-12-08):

# MVP - Brain

Al inicio del proyecto construí una placa de prueba que tenía este aspecto:

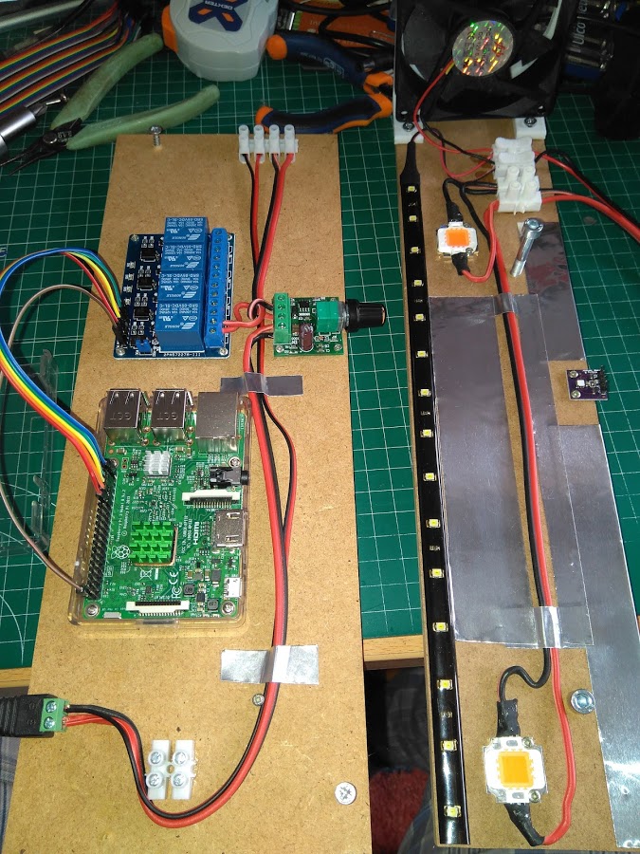
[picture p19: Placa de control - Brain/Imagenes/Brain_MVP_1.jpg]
Brain_MVP_1


A la izquierda tenemos el microordenador **Raspberry Pi 3** con la tarjeta de 4 relés, conectores y regulador de tension para bajar de 12V a un valor inferior  regulable, en esta época estaba ensayando con LEDs soldados a mano. Es lo que vemos en el módulo derecho. No merece  la pena que lo comente en detalle ya que es una vía que aparqué hace un tiempo y que no recomiendo seguir.

Adjunto aquí un diagrama del aspecto aproximado que debe tener la placa de control. Está realizado con el software abierto **Fritzing**:

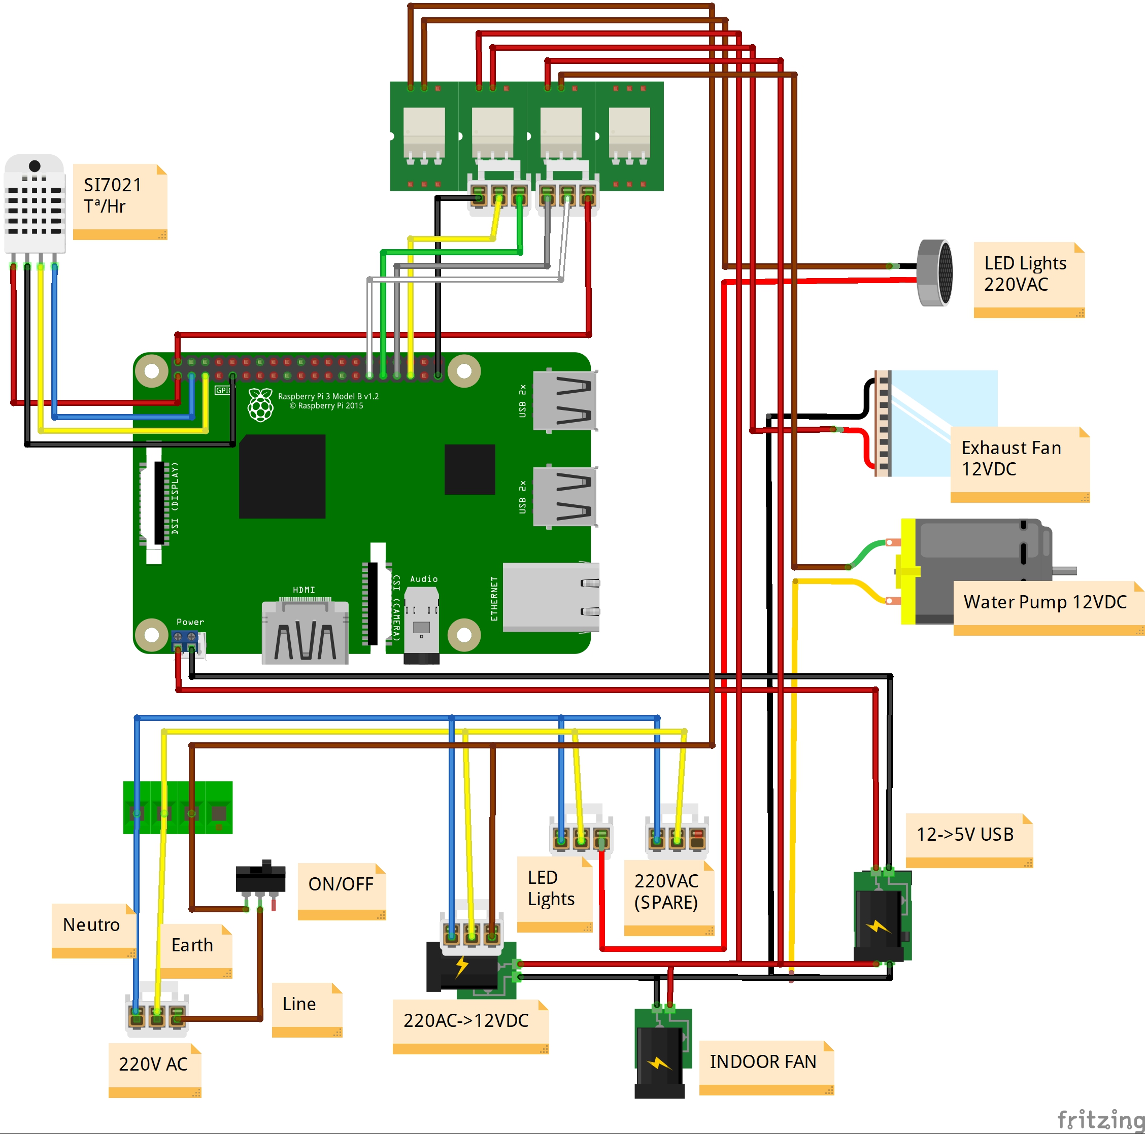
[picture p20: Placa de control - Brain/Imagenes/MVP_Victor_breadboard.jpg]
MVP_Breadboard


El diseño MVP original trabaja con dos de los **4 reles, uno para iluminación y otro para el ventilador que inyecta aire desde el exterior** (cuando la temperatura interior supera un umbral determinado) **En mi diseño se incluye un relé mas, que será para una bomba de 12V para uso de la técnica ebb&flow**. Un relé mas queda de repuesto. Hay otro ventilador siempre conectado a 12V para producir una ventilación interior. Se adaptan los 220V AC a 12V DC para los ventiladores y bomba, de ahí bajamos a 5V USB para la Raspberry, tarjeta de relés y sensor de temperatura/humedad. La iluminación requiere su propia fuente ya que trabaja a tensiones intermedias (normalmente unos 35V DC).

**En esta foto de un Food Computer terminado vemos en el lateral la placa de control unida al chasis**. Todas las piezas están unidas y cubiertas con piezas impresas en 3D que le dan un aspecto mas acabado. La mayor parte del cableado va por canaleta para que no quede a la vista, aunque es inevitable que algo quede visible. Es algo que me gustaría mejorar para futuras versiones:

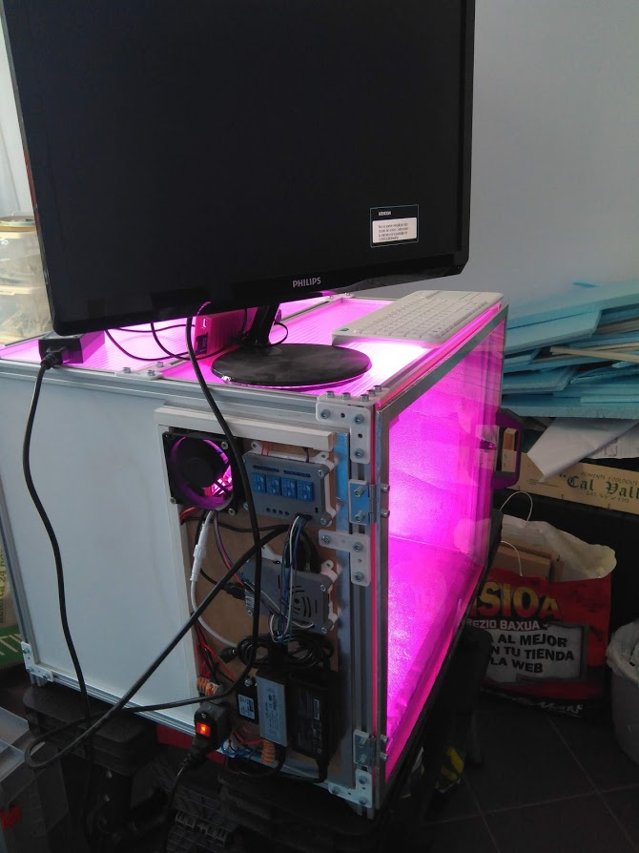
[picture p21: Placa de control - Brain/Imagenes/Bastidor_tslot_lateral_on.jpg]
Brain_fijado a chasis


Aquí vemos varias placas de control en proceso de construcción. Con sus piezas en 3D encima listas para ser ensambladas:

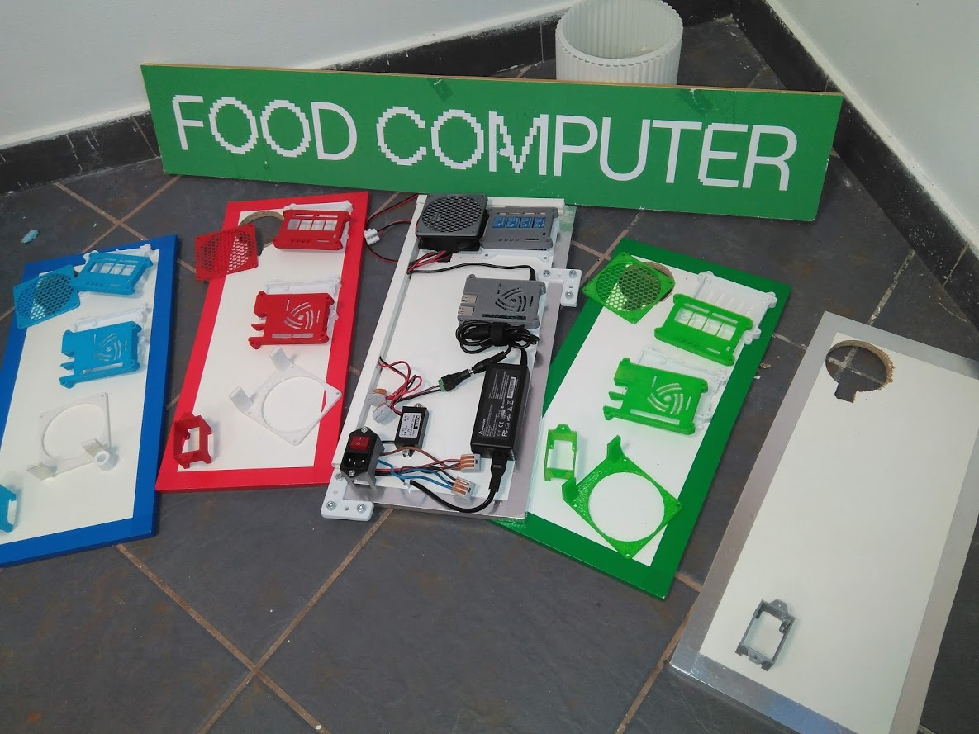
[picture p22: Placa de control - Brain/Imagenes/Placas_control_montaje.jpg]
Brain_montaje


Hay un agujero en el lateral izquierdo para insertar cableado al interior y para entrada del aire del ventilador exterior. En esta foto de una primera versión se colocó la placa en la parte trasera y por ahí se ve la entrada de la cámara USB, sensor de temperatura etc.

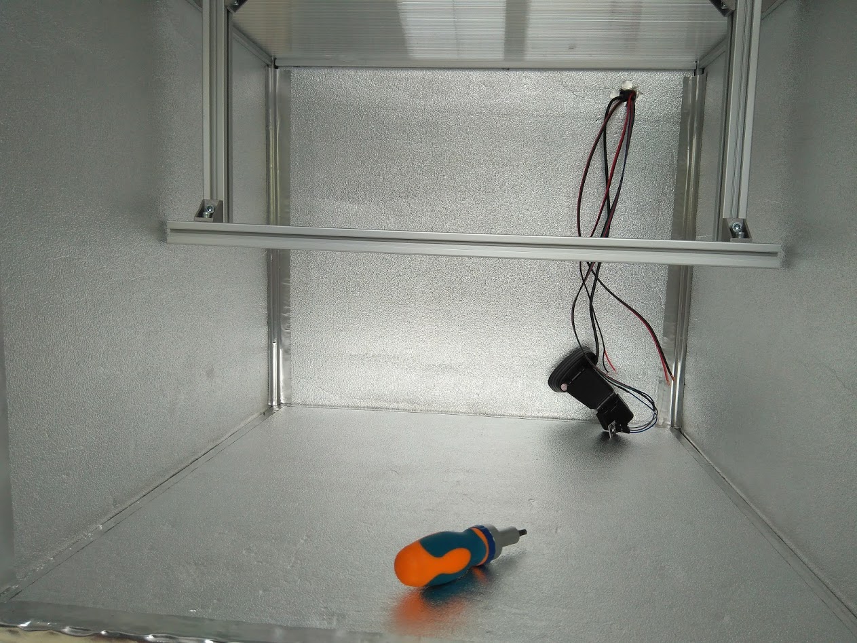
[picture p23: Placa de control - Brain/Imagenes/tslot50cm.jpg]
Brain_cableado_interior


**Una cosa que hecho a la hora de poner el cableado es el de dejar suficiente longitud para poder medir consumos de forma no invasiva** mediante una pinza amperímetrica, como vemos en esta foto. Este es el Food Computer que emplea LED de 40W y lo que vemos es el consumo de corriente a 220V. Vemos que en este tipo de FC es bajo. En equipos mas grandes lógicamente se incrementa.

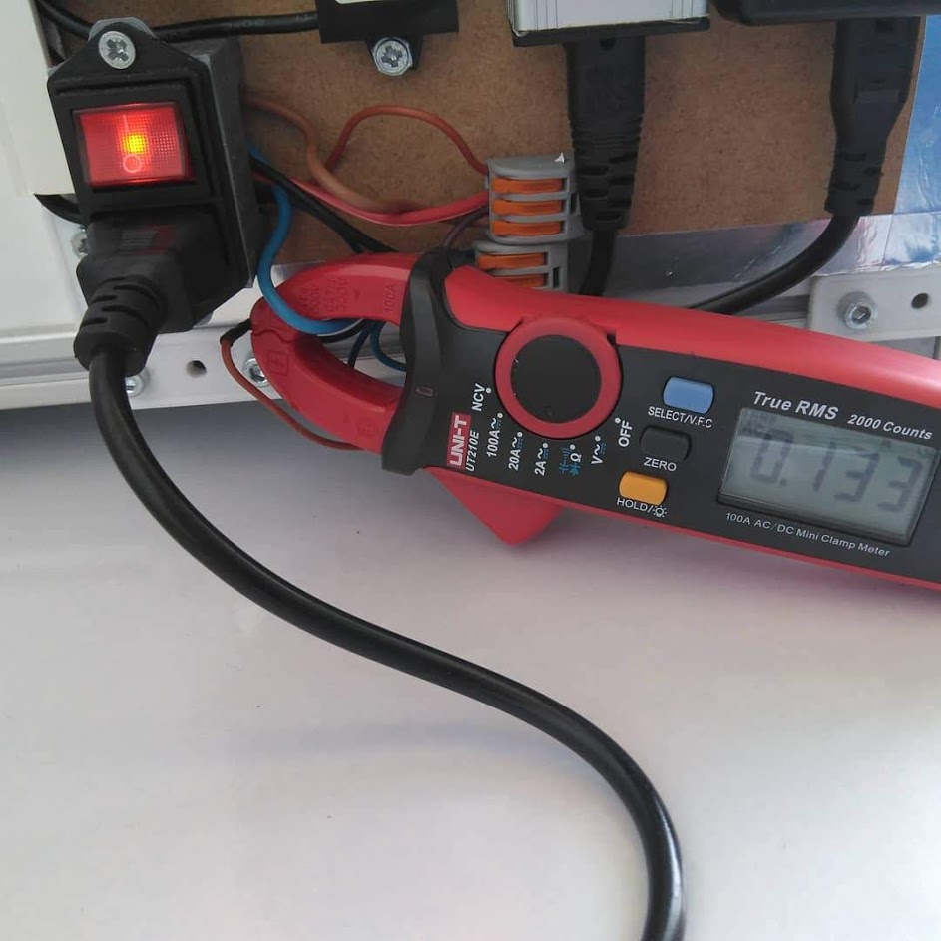
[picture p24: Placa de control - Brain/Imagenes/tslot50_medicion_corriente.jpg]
Brain_medicion_corriente


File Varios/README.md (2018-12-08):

# Varios

Incluyo aquí imágenes del desarrollo del proyecto que no encajan en el resto de apartados y son  **off-topic**

## Impresión 3D de piezas para el proyecto

En la carpeta **STL** están los ficheros correspondientes. Algunos de ellos están impresos a dos colores para mejorar el contraste y acabado. Como vemos aquí:

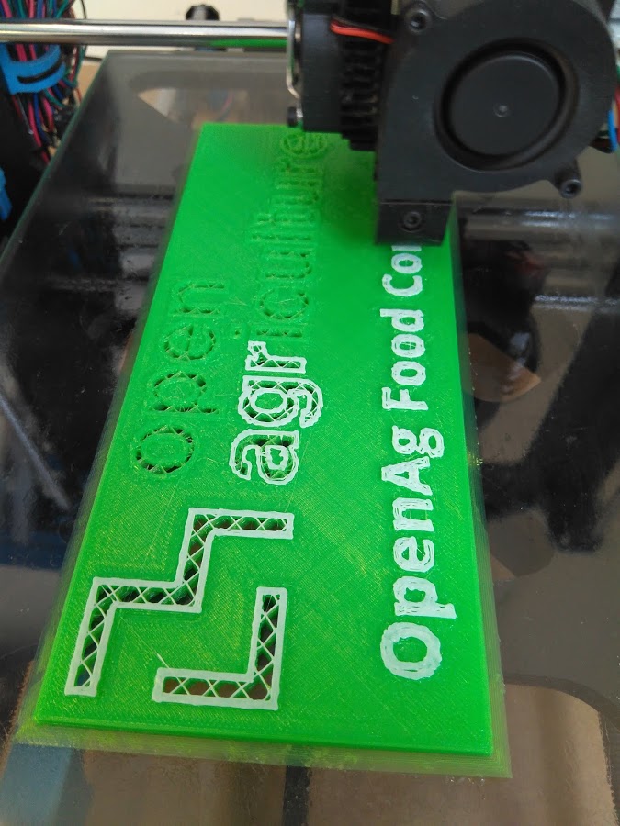
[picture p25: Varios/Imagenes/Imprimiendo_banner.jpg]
Banner
 

En la foto se ve justo el momento en que comienza a imprimir con el segundo color. Una vez terminada la pieza queda así:

Banner 

## Diseñando la granja indoor

Para desarrollar el proyecto he estudiado diferente bibliografía, como este libro sobre **acuaponía**. Debajo vemos un croquis de la granja. Luego ha ido evolucionando.

Croquis 

## El taller

El proyecto lo he desarrollado en un taller de 20m2 que tengo en alquiler en un centro de empresas de **Donostia-San Sebastian**. Aquí trabajo en varios campos y no solo en Food Computers. Aquí vemos un croquis del taller cuando estaba instalando los equipos.

Workshop 

Y aquí una panorámica del taller hace unos meses, está en constante evolución:

Pano_Workshop 

## Evolución de la granja indoor

Algunas fotos para ir viendo el progreso:

Workshop_1 

Workshop_2 

Workshop_3 

Workshop_4 

Workshop_4

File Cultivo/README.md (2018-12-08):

# Cultivo

Se puede cultivar en distintos medios: 

- Suelo "normal" o modificado, pero sólido. **Es el de mi preferencia**.
- Suelo líquido: **hidroponía** . Existen múltiples técnicas, en este proyecto usaremos **DWC** y **ebb&flow**
- Suelo "gaseoso": **aeroponía**, que queda fuera de este proyecto ...  de momento). En este caso se usa una niebla fina de agua mas nutrientes, mediante atomizadores.

El **cultivo hidropónico y aeropónico permite velocidades de cultivo mas altas** y elimina muchos de las plagas por la razón de que no hay un suelo sólido en el que puedan anidar. Muchas plagas en al menos alguna fase deben estar en el suelo. **El incoveniente es que hay que medir de forma frecuente** ciertos parámetros del líquido y debe añadirse lo que le falta. Si no, **el cultivo puede echarse a perder rápidamente.**

**En fincas o instalaciones grandes** donde estas mediciones y dosificaciones se pueden automatizar, y donde se busca la producción alta, **el cultivo hidropónico puede merecer la pena**. **Mi opinión personal es que en instalaciones pequeñas no totalmente automatizadas es mejor usar un medio sólido**. La producción será mas baja pero mas fácil de que llegue a buen término porque si el suelo está en condiciones entregará a la planta todo lo que esta necesita sin necesidad apenas de intervención.

En mi caso he probado varias técnicas porque quiero documentar mínimamente cada una de las fórmulas de cultivo a pequeña escala en un Food Computer.

Paso a explicar entonces los distintos medios.

## En sustrato sólido

He empleado una mezcla de 3 componentes: 
- compost de lombriz
- perlita y/o vermiculita
- fibra de coco

Esto se asemeja al sustrato propuesto en el **método del metro cuadrado** : es un medio sólido, ligero y cargado de nutrientes, con buena aireación y retención del agua. En la foto vemos un cultivo de albahaca en su momento de brotación. Lo iluminamos con luz blanca para comprobar como la planta es verde. Ya que con luz morada se ve de tono oscuro, porque no hay luz verde que la planta puede reflejar.

suelo_solido

Aquí vemos las albahacas cuando ya han crecido, expuesta un momento a la luz del día para ver que son completamente verdes, como no podía ser de otra manera:

albahaca

Y aquí vemos lechuga y hoja de roble creciendo en el mismo medio sólido:

lechuga

## Hidroponía: técnica DWC

DWC significa **Deep Water Culture** y consiste en cultivar en una cubeta llena de agua con los nutrientes. Las raíces siempre están sumergidas en agua, para evitar su asfixia el agua se mantien oxigenada mediante una pequeña bomba de acuario. Esta técnica vale para plantas de pequeño tamaño y crecimiento rápido. Idealmente la mayoría de verduras de ensalada: lechuga, rúcula, canónigo etc.

La base de la planta está alojada en un pequeño cesto insertado en la tapa de la cubeta. Este cesto si contiene un medio sólido donde se coloca la semila para que germine y se desarrolle, de tal forma que las raíces alcanzan el medio líquido y crece a través de el. 

- **Si colocamos en una tapa** se debe vigilar que el nivel de líquido va bajando y se debe reponer, menteniendo la concentración adecuada de nutrientes.
- **Otra manera es colocar una placa de material que flote** y en el van los cestos, normalmente de poliestireno extruido. En este caso aunque el nivel baje las raíces siguen en contacto con el líquido. Hemos de cuidar también el nivel pero no hace falta tener tanto celo.

En la foto que sigue vemos los cestos y el medio sólido empleado, en mi caso he usado fibra de coco pero hay otras soluciones.

Germinado

La planta brotará y crecerá con normalidad como vemos aquí. Podemos ver que esta cubeta tiene bastante agujeros, concretamente 24. En mi experiencia he visto que es mejor tener menos, de 6 a 12. Para evitar la entrada de luz en esos agujeros (puede provocar que se formen algas) se pone un material completemente opaco, como retales de plastico aluminizado.

Brotes

Pasado un tiempo podemos ver el sistema radicular flotando en el agua si levantamos la tapa, tal y como vemos en esta foto:

Raices

Aquí vemos el cultivo bastante desarrollado, tanto en medio sólido como DWC: 

Primer_cultivo_ok

Por este sistema se pueden cultivar plantas de mayor porte como tomates, berenjenas o pimientos, pero requieren entutorado. Aquí vemos algunas fotos:

Tomate_I

Tomate_II

## Hidroponía: técnica Ebb&Flow

**En proceso de pruebas y documentación**

## Hidroponía: instrumentación necesaria

Para cultivos a pequeña escala necesitamos fundamentalmente dos instrumentos:

- Medidor de **pH** :  De su valor óptimo depende que las plantas puedan absorber las sales minerales y los nutrientes necesarios.
- Medidor de conductividad **EC** : indica el nivel de concentración de nutrientes disueltos en el agua.

Aquí vemos ambos medidores, existen en el mercado equipos bastante baratos, en la banda de los 25euros:

Instrumentacion

**La preparación del medio de cultivo** se hace añadiendo la dosis exacta de material sólido que se debe disolver en el agua, de tal forma que los valores de ph y conductividad sean los correctos. Normalmente se emplea una solución **A+B** (así se llama), que contiene todas las sales necesarias, unas 17, las que la planta necesita para crecer. Esta solución se vende en diferentes cantidades.

En mi caso y con el sobre plastificado que se ve en la foto se prepara una botella de 1,5l. Asi que vale con cualquier botella estandar de agua. Es importante protegerla de la luz y agitar bien siempre antes de utilizar. Para hacerla opaca he empleado cinta de carrocero gris. El líquido que queda es de color morado, se ve en el vaso dosificador. Una botella de 1,5 litros permite preparar 200 litros de agua para cultivo. En esta cubeta caben unos 10l. asi que con el contenido del vaso es suficiente.

A+B_dosificacion

Hemos de vigilar el nivel de líquido de la cubeta y reponerlo periodicamente, asi como vigilar los valores de EC y PH con una frecuencia mínima semanal. Se recomienda vaciar la cubeta y reponerla entera con la dosificación correcta para garantizar que las concentraciones de nutrientes son los adecuados.

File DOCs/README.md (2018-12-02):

# Documentos

En esta carpeta encontrarás varios documentos en formato PDF para ampliar información sobre técnicas de cultivo en hidroponía, vertical farming, iluminación etc. 

La mayoría están en inglés.

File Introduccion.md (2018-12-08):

# Food-Computer-a-la-guipuzcoana

## El contexto

El concepto surgió al visitar Fukushima y ver que nunca se podría cultivar allí debido a la contaminación de las tierras. De ahí se vió que hay muchos contextos en los que el cultivo resulta díficil y una tecnología de este tipo podría ayudar.

**El propósito es garantizar el cultivo de aproximadamente el 30% de alimentos para consumo humano de forma local**, sean cuales sean las condiciones climáticas o del suelo. De este modo se podría cultivar en lugares como Fukushima (con tierras contaminadas radiactivamente), la Antártida, o incluso en el espacio. Y sin ir tan lejos, se pueden utilizar azoteas y espacios urbanos actualmente en desuso. El aporte directo y local de estos alimentos, normalmente muy perecederos, permite enriquecer la dieta de las personas que los utilizan.

Hay que tomar en cuenta el incremento de la población mundial que alcanzará los 9000 millones de personas en torno a 2040. Y al tiempo la destrucción y erosión de tierras de cultivo. Habrá que administrar las tierras de tal forma que los campos queden para cultivos extensivos o que requieren espacio, mientras que los cultivos mas pequeños y de ciclo corto se puedn cultivar localmente mediante estas técnicas, incluso de forma vertical.

## Diseño y detalles constructivos

El concepto FC utiliza el cultivo hidropónico, concretamente **DWC (Deep Water Culture)** que permite cultivar verduras de ensalada de pequeño tamaño y ciclo corto. El MIT está ensayando ahora otros cultivos que emplean técnicas alternativas e incluso cultivo con suelo para plantones de avellano, etc.

Aunque el diseño original es cerrado y no recibe luz exterior, nada nos impide hacerlo parcialmente transparente para que tenga una iluminación mixta. Es así como estoy diseñando mis modelos, de esta manera reduciremos el consumo eléctrico del equipo, utilizando la luz artificial solo cuando hace falta.

Una vez definidos una serie de características del equipo veamos las escalas de tamaño a las que el MIT se ha propuesto trabajar:

- **Food Computer** Es la unidad mas pequeña, de un tamaño de 80x50x80cm aproximadamente, para ser colocada sobre un escritorio. Capacidad de cultivo muy reducida y solo para propósitos de investigación y educación.
- **Food Server** Tiene el tamaño de un contenedor marítimo y la capacidad de producir alimentos para una familia o bien para abastecer a un pequeño restaurante
- **Food Data Center** Tiene el tamaño de una fábrica, el tamño aquí es indeterminada ya que a esta escala no se ha desarrollado todavía.

En este contexto tenemos también el concepto de **Climate Recipe o Receta Climática**: Es un fichero de formato plano que contiene los datos necesarios para que un Food Computer pueda reproducir un determinado clima apto para un cultivo. Estandarizar este formato permitiría que se puedan homologar experimentos de cultivo en todo el mundo.

El equipo tiene los siguientes **sensores**:
- Temperatura y humedad del aire
- Temperatura del agua de cultivo
- Niveles de CO2 en el aire
- EC o conductividad del agua (indicativo de concentración de sales de cultivo)
- PH , indicativa de la capacidad de absorción de nutrientes disueltos
- imágenes mediante cámara, se hace un timelapse que con técnicas de **machine learning** permite analizar el crecimiento de la planta y si este es correcto.

Y por otro lado, tiene los siguientes **actuadores:**
- **water chiller** para controlar la temperatura del agua de cultivo: hay que mantenerla lo bastante baja para mantener altos los niveles de oxígeno disuelto asi como la proliferación de hongos y/o bacterias en el agua. Al tiempo que la temperatura del aire puede ser diferente por completo.
- Bomba de aire para crear burbujas y oxigenar el agua del cultivo
- Ventilador para mantener corrientes de aire en la cámara y evitar condensaciones o puntos donde proliferen los hongos o plagas.
- Ventilador exterior que ventea la cámara si esta alcanza una temperatura inadecuada, o para equilibrar niveles de CO2. Puede emplearse un módulo Peltier para calentar o enfriar el aire.
- Iluminación LED : se regula su tiempo de encendido. En los últimos desarrollos del MIT se está controlando también el espectro luminoso(mayor o menor proporción de rojo, IR etc)
- Bombas peristálticas que inyectan nutrientes al agua, asi como reguladores del ph.

**Las versiones EDU y MVP** son mas sencillas y disponen de menos sensores y actuadores para facilitar la construcción, uso y mantenimiento. Asimismo tienen un precio bastante mas asequible que permitirá su rápida extensión.

## Un poco de historia...

**El proyecto es liderado por Caleb Harper del MIT.**

**El proyecto Food Computer en su forma original desarrolló dos versiones, la V1 y la V2**, bastante similares entre si. Era un equipo caro con un coste de materiales en torno a los **2500$**, al que había que añadir la mano de obra. Era complicado de construir y con muchos problemas tanto hardware como software. Contaba con mucha instrumentación y estaba orientado a centros de I+D.

La comunidad tenía dificultades para construirlo. Debido a la imposibilidad de dar soporte a los problemas técnicos por parte de **Open AG (MIT)** y a que ellos estaban desarrollando otros proyectos, **finalmente decidieron parar  su desarrollo en Marzo de 2018**. La información sigue estando disponible en Internet pero ya no cuenta con soporte.

Ellos se han centrado en el desarrollo del **Food Server** , del tamaño de un contenedor marítimo, **para cultivos de mayor cantidad o incluso cultivos experimentales como el algodón o el avellano.**

Han estado en contacto con la comunidad, particularmente con la educativa, ya que desean que esta tecnología llegue a la escuelas. Y finalmente han sacado un  modelo nuevo llamado **PFC EDU 3.0** Este es mas pequeño y sencillo, costando en torno a los 500$. Ha  salido en Noviembre 2018 y de momento las unidades que se han fabricado están en manos exclusivas del MIT, que ha liberado los planos para que la comunidad pueda hacerlo, aunque es pronto todavía. 

Quizás la mayor dificultad es la fabricación de la placa base, de unos 30x30cm, donde insertará una placa **Beaglebone Black Wireless** en sustitución de la **Raspberry Pi 3** .

Desde el año 2017, en la comunidad se ha ido construyendo una alternativa llamada **MVP**, similar al **EDU** y que está en la banda de los 300$. Es la base sobre la que se ha construido todo este proyecto ya que reune la mayoría de los requisitos necesarios.

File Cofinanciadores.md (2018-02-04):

**A continuación cito a todas las personas que han apoyado al desarrollo de este proyecto.**

Doy las gracias a la Diputación Foral de Gipuzkoa por su apoyo a través del programa META! y a todas las personas que han donado y han pedido el anonimato.

# Agradecimiento con mención de honor para las siguientes personas:

**eltercerlugar**

**Fulgencio Bermejo**

**Antonio Padilla**

**manuel "Leobot"**

**Juan Gonzalez Gomez "Obijuan"**

**Ana Digón**

**Victoria Eugenia Marcos Maldonado**

**Mikel Serrano "Mitzilister"**

**Ioaki**

**pang**

**Hodei Arrausi**

**Miguel torres**

**María Barahona**

**Alfonso Matute**

**Josu Redondo (Plabs 3D)**

**Enrique Martinez**

**NEIKER**

**Ana Martín Elizondo**

**Nuria Robles**

**Yokin Lodos Calvo**

**Miguel A. Campanero**

**Maria Jesus Barrenechea Barahona**

**Ander Garay**

**A3Z Advanced**

## Agradecimiento por su colaboración a las siguientes personas:

Adrián Torres Omaña

José Fernando

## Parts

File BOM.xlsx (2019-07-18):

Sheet: Distribucion
 |  |  |  |  |  | LACK 50x50x50
 |  |  |  |  | BRAIN | GROW LED 40W
 | TSLOT 100x100x50 |  |  | TSLOT 50x100x50 |  | TSLOT 50x50x50
BRAIN | GROW LED 85W |  | BRAIN | LED CFL (4x16W) | BRAIN | GROW LED 40W
 | GROW LED 85W
 | SHELF 120x90x50 (2 LEVELS) |  |  | SHELF 120x90x50
BRAIN |  | GROW LED 300W | BRAIN | GROW LED 2x85W

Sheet: BOM resumen
BOM RESUMEN
 |  |  | MVP 50 |  | MVP100 |  | MVP200 |  | MVP LACK |  | SHELF1-2 |  | SHELF3
Descripcion Frame | Proveedor | Coste/ud | Cantidad | Subtotal | Cantidad | Subtotal | Cantidad | Subtotal | Cantidad | Subtotal | Cantidad | Subtotal | Cantidad | Subtotal
Perfiles Tslot 20cm | Motedis | 0.7 | 1 | 0.7 | 2 | 1.4 | 2 | 1.4
Perfiles Tslot 50cm | Motedis | 1.6 | 15 | 24 | 9 | 14.4 | 6 | 9.6
Perfiles Tslot 100cm | Motedis | 3.1 | 0 | 0 | 6 | 18.6 | 10 | 31
Panel Dm blanco 3mm (plancha 1,20x0,60m) | AKI/LM | 5 | 1.5 | 7.5 | 3 | 15 | 4 | 20
Base DM 1cm (plancha 1,20x0,60m) | AKI/LM | 10 | 0.5 | 5 | 0.5 | 5 | 1 | 10
Tornilleria | AKI/LM | 5 | 1 | 5 | 1 | 5 | 1 | 5
Plancha policarbonato de 6mm (plancha de 2x1m) | AKI/LM | 35 | 0.125 | 4.375 | 0.125 | 4.375 | 0.5 | 17.5
Forro porexpan 3mm con reflectante (carrete de 6m) | Bricodepot | 16 | 0.3 | 4.8 | 0.5 | 8 | 0 | 0
Mylar reflectante (rollo 120cm x 10m) | Amazon | 35 | 0 | 0 | 0 | 0 | 0.3 | 10.5
Cinta aluminio (carrete de 15m) | AKI/LM | 8 | 0.5 | 4 | 0.75 | 6 | 1 | 8
Plancha metacrilato 4mm para puerta (plancha 1x0,5m) | AKI/LM | 15 | 0.5 | 7.5 | 1 | 15 | 0 | 0
Film semireflectante | Amazon | 12 | 0.3 | 3.6 | 0.6 | 7.2 | 1.25 | 15
Piezas impresas en 3D | -- | 15 | 1 | 15 | 1 | 15 | 1 | 15
Pomo, bisagras, iman, etc | Motedis | 10 | 1 | 10 | 1 | 10 | 1 | 10
Subtotal Frame |  |  |  | 91.475 |  | 124.975 |  | 153
Descripcion Vitaminas
Raspberry Pi 3 | Amazon | 35 | 1 | 35 | 1 | 35 | 1 | 35
disipadores R-Pi, caja, fuente AC | Amazon | 10 | 1 | 10 | 1 | 10 | 1 | 10
Tarjeta SD 32GB | Amazon | 15 | 1 | 15 | 1 | 15 | 1 | 15
Tarjeta de 4 reles | Banggood | 10 | 1 | 10 | 1 | 10 | 1 | 10
cableado, bornas, regletas | Banggood | 5 | 1 | 5 | 1.5 | 7.5 | 2 | 10
conector (jack 12V, tripolares para AC etc) | Banggood | 5 | 1 | 5 | 1 | 5 | 1 | 5
Fuente DC 12V | Amazon | 15 | 1 | 15 | 1 | 15 | 1 | 15
sensor temp y humedad SI720 | Banggood | 4 | 1 | 4 | 1 | 4 | 1 | 4
webcam | Amazon | 20 | 1 | 20 | 1 | 20 | 1 | 20
luces LED (W) | Amazon | -- | 40 | 40 | 60 | 50 | 85 | 80
ventilador circulacion | Amazon | 3 | 2 | 6 | 2 | 6 | 2 | 6
Solucion A+B | Amazon | 15 | 1 | 15 | 1 | 15 | 1 | 15
PH + EC-TDS | Amazon | 15 | 1 | 15 | 1 | 15 | 1 | 15
kit hidroponia básico | Banggood | 30 | 1 | 30 | 1 | 30 | 0 | 0
Bomba acuario 12VDC | Amazon | 12 | 0 | 0 | 0 | 0 | 1 | 12
Cajas uso alimentario (4 cajas, 2 superiores y 2 inferiores) | Rajapack | 30 | 0 | 0 | 0 | 0 | 1 | 30
Sustrato (perlita o arlita) | Alkain | 15 | 0 | 0 | 0 | 0 | 1 | 15
tubos 16mm, Ts, codos, aspersores etc | AKI/LM | 20 | 0 | 0 | 0 | 0 | 1 | 20
Subtotal Vitaminas |  |  |  | 225 |  | 237.5 |  | 317
Total de materiales (Frame mas vitaminas) |  |  |  | 316.475 |  | 362.475 |  | 470
Mano de Obra |  | 25 | 20 | 500 | 25 | 625 | 30 | 750
TOTAL |  |  |  | 816.475 |  | 987.475 |  | 1220

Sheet: MVP 50x50x50
FC MVP 0,5x0,5x0,5 m |  | Tamaño >> | 50x50x50 | CM
Descripcion | Cantidad | Proveedor | Coste/ud | Subtotal
Perfiles Tslot 50cm | 14 | Motedis | 3.5 | 49
Perfiles TSLOT20cm | 2 | Motedis | 0.7 | 1.4
Panel Dm blanco 3mm (plancha 1,20x0,60m) | 1.5 | AKI/LM | 5 | 7.5
Base DM 1cm (plancha 1,20x0,60m) | 0.5 | AKI/LM | 10 | 5
Tornilleria | - | AKI/LM | - | 0
Plancha policarbonato de 6mm 0,5x0,5m (plancha de 2x1m) | 0.125 | AKI/LM | 35 | 4.375
Forro porexpan 3mm con reflectante (carrete de 6m) | 0.3 | Bricodepot | 16 | 4.8
Cinta aluminio (carrete de 15m) | 0.3 | AKI/LM | 8 | 2.4
Plancha metacrilato 4mm para puerta (plancha 1x0,5m) | 0.5 | AKI/LM | 15 | 7.5
Pomo, bisagras, iman, etc | 1 | Motedis | 6 | 6
Subtotal Frame |  |  |  | 87.975
Raspberry Pi 3 | 1 | Amazon | 35 | 35
disipadores R-Pi, caja, fuente AC | 1 | Amazon | 10 | 10
Tarjeta SD 32GB | 1 | Amazon | 15 | 15
Tarjeta de 4 reles | 1 | Banggood | 8 | 8
cableado, bornas, regletas | 1 | Banggood | - | 0
conector jack 12V | 1 | Banggood | 1 | 1
sensor temp y humedad SI720 | 1 | Banggood | 3 | 3
webcam | 1 | Amazon | 15 | 15
luces LED | 1 | Amazon | 40 | 40
ventilador circulacion | 2 | Amazon | 3 | 6
Solucion A+B | 1 | Amazon | 15 | 15
PH + EC-TDS | 1 | Amazon | 15 | 15
kit hidroponia básico | 1 | Banggood | 25 | 25
Subtotal Vitaminas |  |  |  | 188
Total del conjunto |  |  |  | 275.975

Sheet: MVP 50x100x50
FC MVP 0,5x1x0,5 m |  | 50x100x50
Descripcion | Cantidad | Coste/ud | Subtotal

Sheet: MVP 100x100x50
FC MVP 01x01x0,5 m |  | 100x100x50
Descripcion | Cantidad | Coste/ud | Subtotal

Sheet: LACK
FC MVP LACK 0,5x0,5x0,5 m |  | 50x50x50
Descripcion | Cantidad | Coste/ud | Subtotal

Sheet: SHELF 1-2
FC MVP 1,2x0,9x0,5 m |  | 120x90x50
Descripcion | Cantidad | Coste/ud | Subtotal

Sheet: SHELF 3
FC MVP 1,2x0,9x0,5 m |  | 120x90x50
Descripcion | Cantidad | Coste/ud | Subtotal

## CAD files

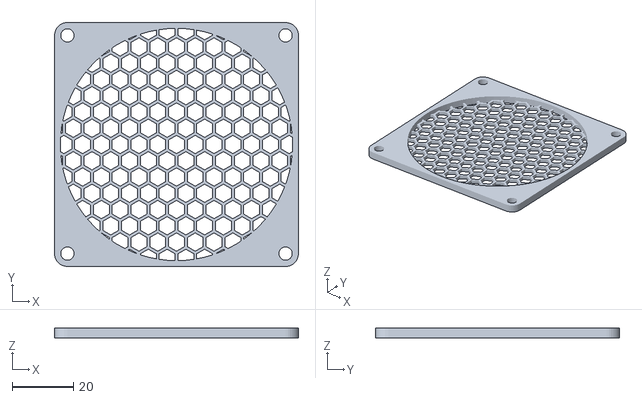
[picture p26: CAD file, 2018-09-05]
STL/Thingiverse/80mm_honeycomb_full_fan_cover.stl
80.0 x 80.0 x 3.20

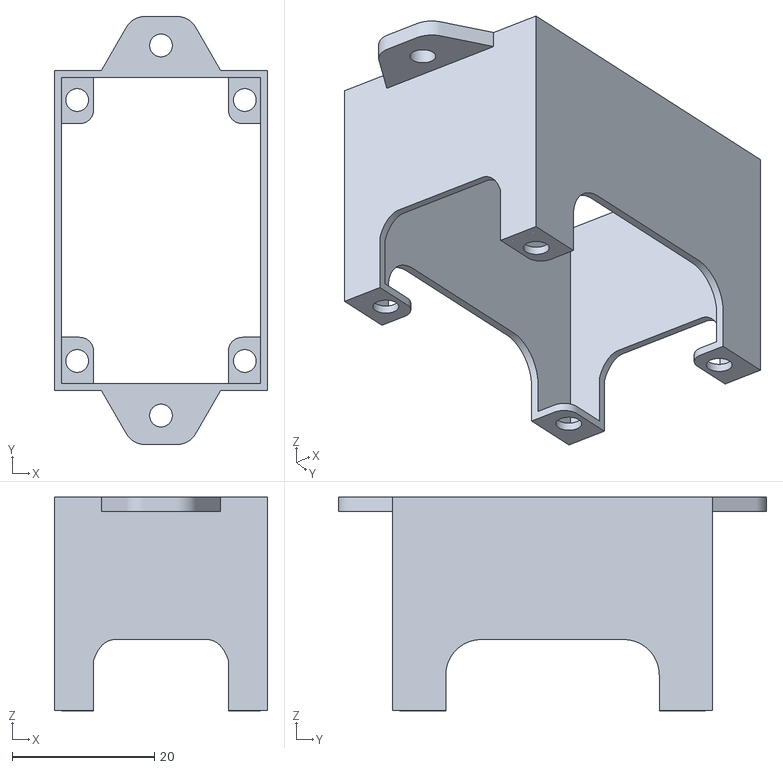
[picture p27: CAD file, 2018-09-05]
STL/Soporte interruptor ac.stl
30.0 x 60.1 x 30.0

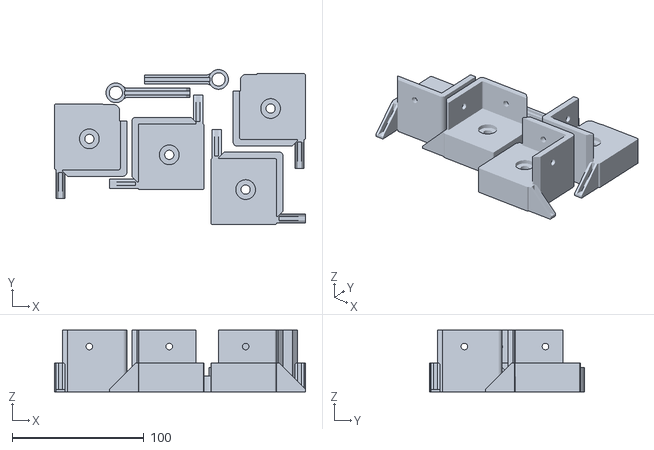
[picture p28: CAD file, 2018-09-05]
STL/Thingiverse/Prusa_Enclosure_Top_Corners.stl
190.8 x 117.7 x 47.0

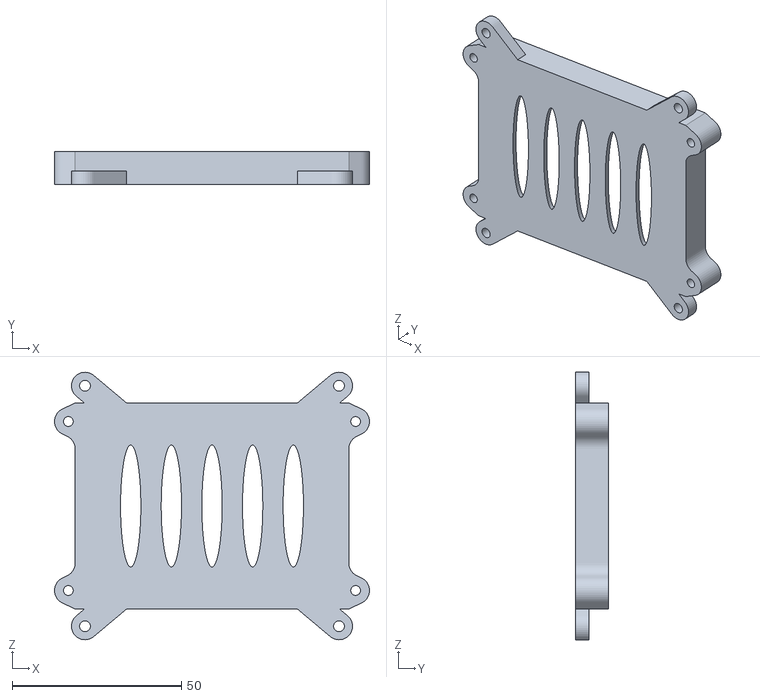
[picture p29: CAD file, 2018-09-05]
STL/Thingiverse/relay_case_bottom.STL
93.0 x 9.75 x 79.0

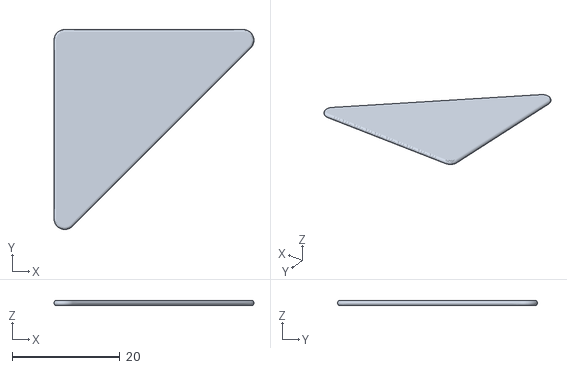
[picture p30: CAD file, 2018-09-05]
STL/Tope pieza porexpan.stl
37.2 x 37.2 x 1.00

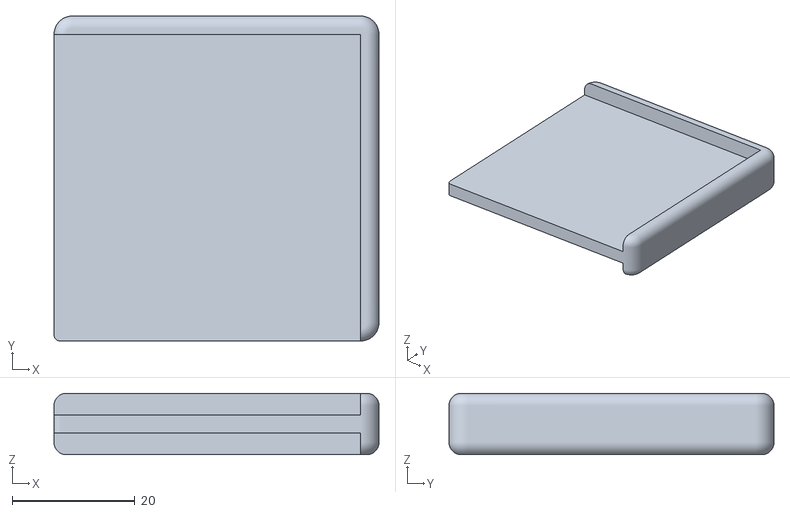
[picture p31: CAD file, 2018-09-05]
STL/resalte-patas.stl
53.0 x 53.0 x 10.0

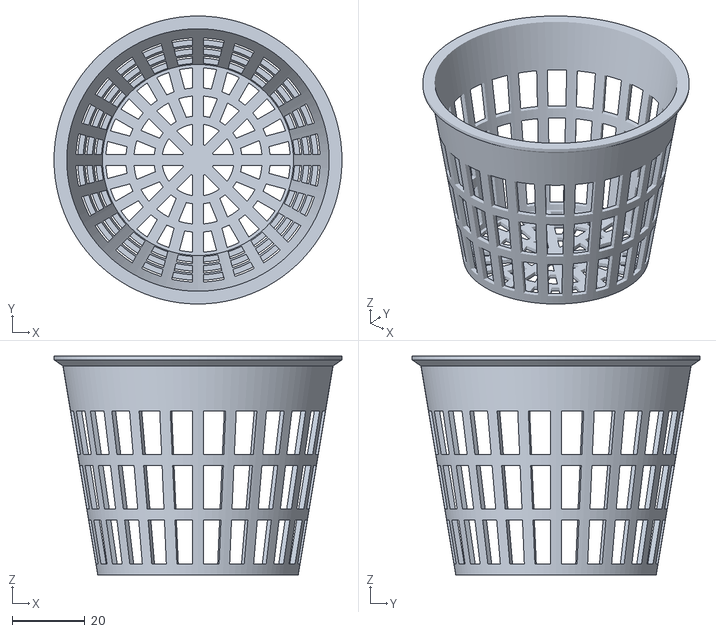
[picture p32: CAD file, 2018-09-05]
STL/Thingiverse/parametric-net-pot.stl
79.0 x 79.0 x 60.0

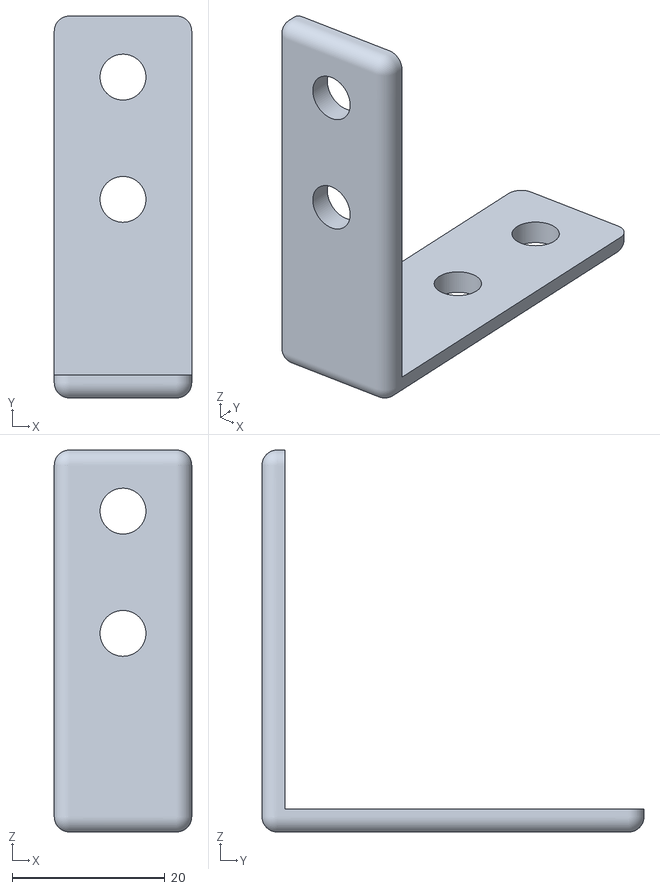
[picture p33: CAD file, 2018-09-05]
STL/Escuadra exterior.stl
18.0 x 50.0 x 50.0

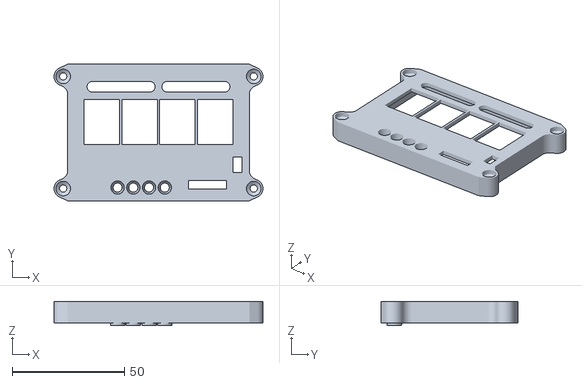
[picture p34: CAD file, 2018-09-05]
STL/Thingiverse/relay_case_top.STL
93.0 x 60.8 x 10.9

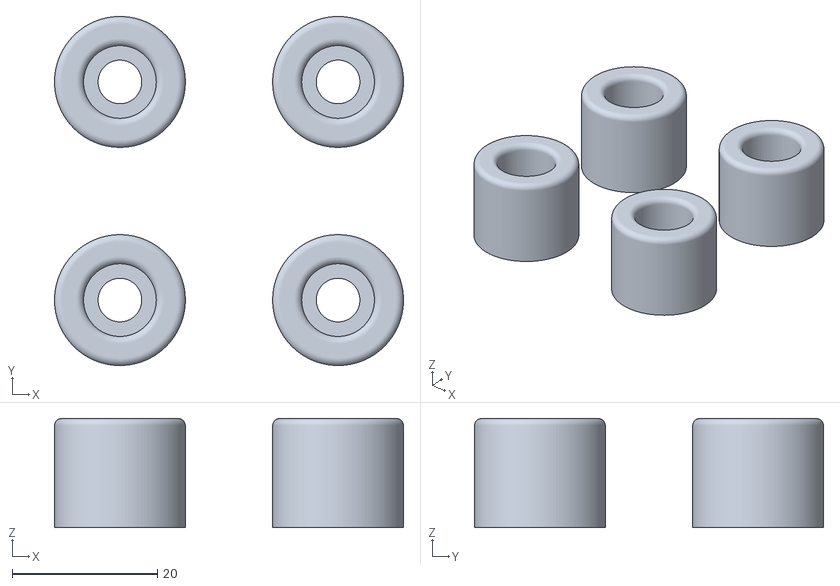
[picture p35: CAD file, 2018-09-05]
STL/4xDampers.stl
48.0 x 48.0 x 15.0

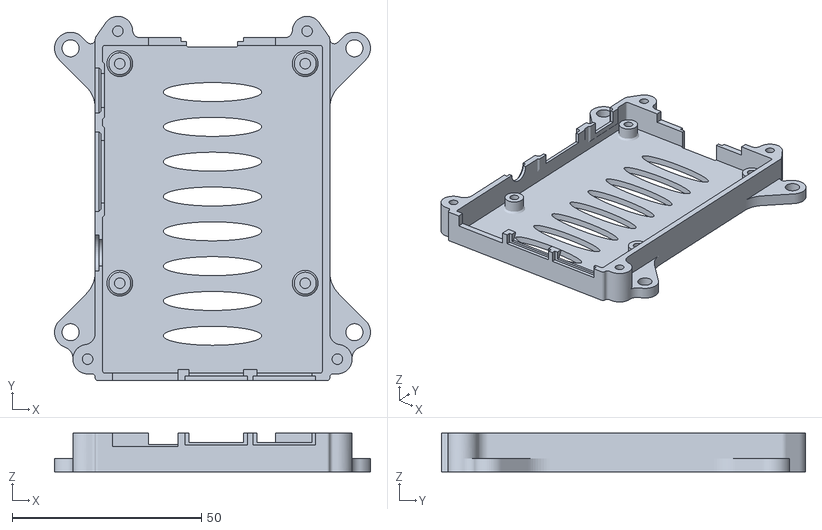
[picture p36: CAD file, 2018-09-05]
STL/Thingiverse/rpi3-bottom_netfabb.stl
83.5 x 96.2 x 10.3

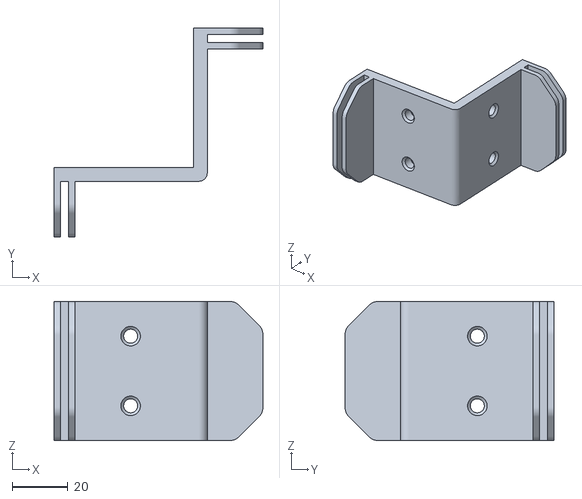
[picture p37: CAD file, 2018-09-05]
STL/acople-patas.stl
75.0 x 75.0 x 50.0

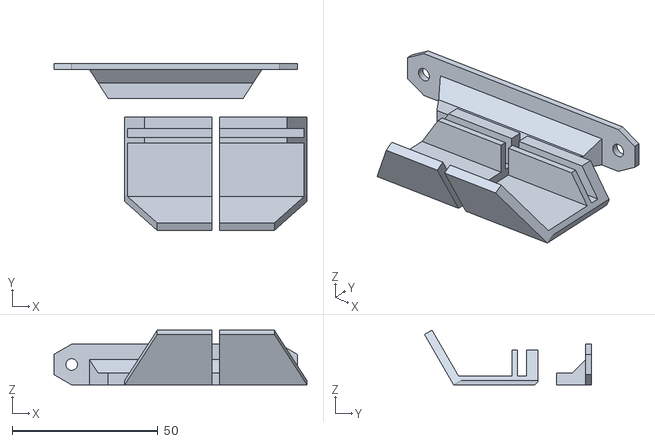
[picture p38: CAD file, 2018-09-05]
STL/Thingiverse/Prusa_Enclosure_Door_Knob.stl
86.9 x 57.4 x 18.8

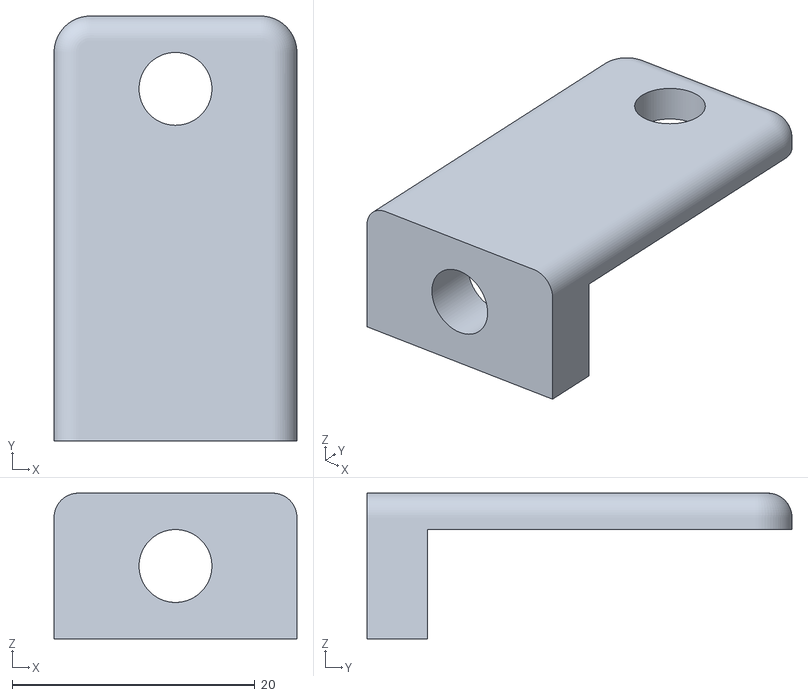
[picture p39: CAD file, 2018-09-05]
STL/acople_bisagra_policarb.stl
20.0 x 35.0 x 12.0

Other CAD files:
STL/Placa electronica.stl
STL/Thingiverse/Tweezers_type_1.stl
STL/Thingiverse/Prusa_Enclosure_Cable_clip.stl

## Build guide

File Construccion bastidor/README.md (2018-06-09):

# Construcción del bastidor

El bastidor debe cumplir la función de aislar los cultivos del exterior, manteniendo la temperatura y humedad adecuadas. Así que debe tener una buena capacidad de aislamiento térmico. Asimismo debe ser reflectante en su interior, para poder aprovechar al máximo la luz artificial que hemos de generar.

Debe tener varios puntos para fijar los componentes, sensores, cámara, etc.

Debe ser resistente pero al mismo tiempo si es liviano, mejor que mejor.

Si se va a usar en espacios sin luz puede ser completamente opaco al exterior, pero es conveniente que la parte superior sea transparente y asi puede usar luz natural si se da el caso. Para esto empleo policarbonato, es un material transparente de cierto espesor con cámara de aire, y por tanto un buen aislante térmico.

La puerta de acceso frontal debe ser de apertura fácil y puede ser total o parcialmente transparente para ver su interior sin necesidad de abrirla. Habitualmente tienen una pequeña ventana. Es conveniente que tenga un recubrimiento interior semireflectante, esto permite que la luz rebote en su interior y no se pierda, pero al tiempo podemos ver a través de ella. También reduce la luz que sale al exterior y evita el deslumbramiento, la luz que se genera es muy brillante y puede causar ceguera parcial si la miramos directamente.

Existen varias maneras de construir un bastidor en funcion de los materiales y coste disponible. Se desglosan a continuación:

## Con cajas de carton:

Construcción con caja de cartón de 60x40x40 cm. 

[Ver detalles aquí:](Bastidor_carton.md)

## Con perfiles de aluminio:

Construcción con perfiles de aluminio TSLOT de 2020 y ranura de 6mm.

[Ver detalles aquí:](Bastidor_aluminio.md)

## Con mueble LACK de Ikea

Construcción usando como frame un mueble LACK de Ikea (o dos unidos entre si).

[Ver detalles aquí:](Bastidor_LACK.md)

## Con estanterías metálicas

A partir de estanterías metálicas se puede construir un bastidor muy grande y de las medidas que queramos.

[Ver detalles aquí:](Bastidor_estanteria.md)

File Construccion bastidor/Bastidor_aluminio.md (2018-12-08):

# Bastidor con perfiles de aluminio

Se trata de construir el bastidor con perfiles de aluminio **TSLOT** de 20x20mm y ranura de 6 mm. Se pueden comprar con  la longitud cortada a la medida que queramos, aunque es mejor usar valores mas o menos estandar. Estos perfiles son relativamente baratos, asi que **el coste total del bastidor es bajo, al tiempo que conseguimos una estructura ligera y rígida, con un aspecto muy profesional**.

**A continuación mostraré como montar un bastidor de 50x50x50cm** pero modificando las dimensiones se puede hacer d elas dimesniones que se quiera, de hecho he construido otros dos de 50x50x100 y 100x50x100 para probar diferentes factores de forma y comparar los resultados. Si quieres ver fotos de los mismos los tienes aquí:

[MVP de aluminio 50x50x100](Bastidor_50x50x100.md)

[MVP de aluminio 50x100x100](Bastidor_50x100x100.md)

Veamos en esta primera foto el aspecto que tiene el bastidor:

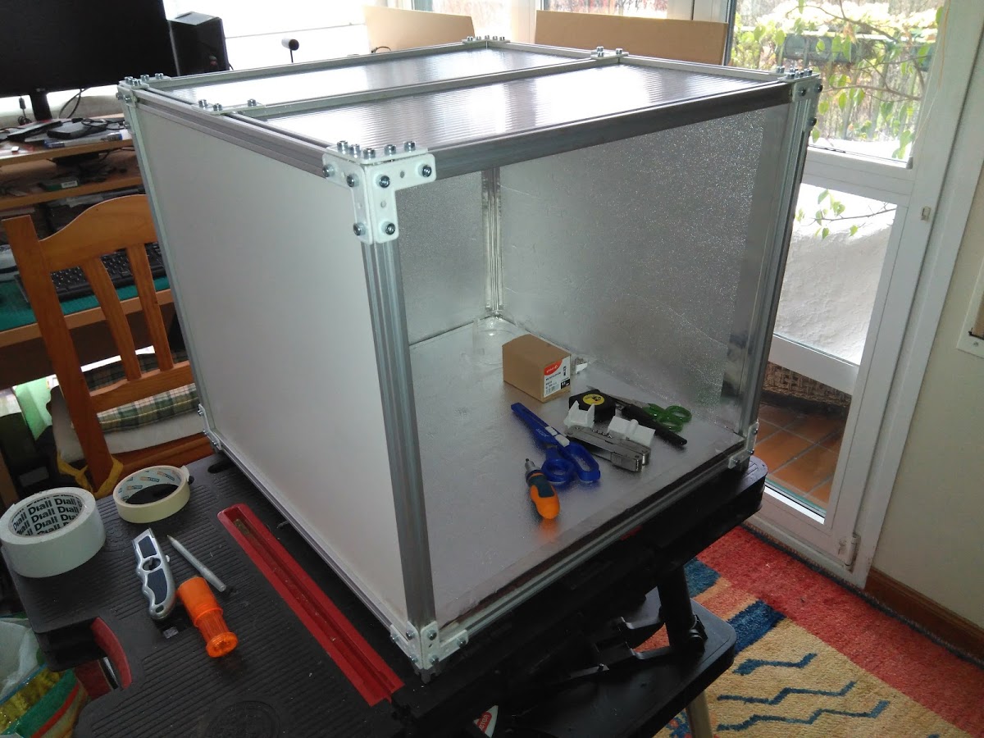
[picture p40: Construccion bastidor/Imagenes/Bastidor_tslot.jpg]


Como es un cubo tenemos 12 piezas de 50cm, mas otra situada en la mitad de la cara superior y que sirve para "atar" cosas internamente. Veremos eso mas adelante. Asi que **tenemos un total de 13 piezas de 50cm**.

**La unión entre aristas se hace mediante unas piezas impresas en 3D** en forma de L o de T, con tornillos de 5x8mm y tuercas martillo de 5mm.

**Las facetas se cubren con dos capas de material** unidas con cinta adhesiva de doble cara. Las dos capas son las siguientes:

- Capa de **madera DM de 3mm**, con un lado plastificado en blanco.
- Capa de **poliestireno de 3mm**, con una capa cubierta de aluminio mate ( este material se usa para aislamiento en radiadores)

Ambas suman unos 6mm asi que insertan en la ranura correctamente, se meten desde arriba con la arista superior quitada y luego se fija, quedando la faceta integrada con las aristas. Si vemos un poco de holgura podemos meter trocitos de madera DM o de poliestireno que han sobrado desde el interior, a modo de cuña, en la ranura y asi quedará perfecto.

**La parte superior está hecha de dos piezas de policarbonato alveolar**, que es transparente y permite el paso de la luz. Asimismo proporciona un buen aislamiento térmico debido a los alvéolos de aire que tiene en su interior.

**La base debe ser resistente al peso, para ella empleamos un trozo de madera DM de 1cm** de espesor, cubierta con el mismo poliestireno aluminizado de 3mm.

Rematamos las aristas en el interior con un poco de cinta adhesiva de aluminio y nos queda el aspecto que vemos en la foto.

En el frontal ponemos un poco de burlete para sellar el cierre de la puerta, como vemos en la foto que sigue. 

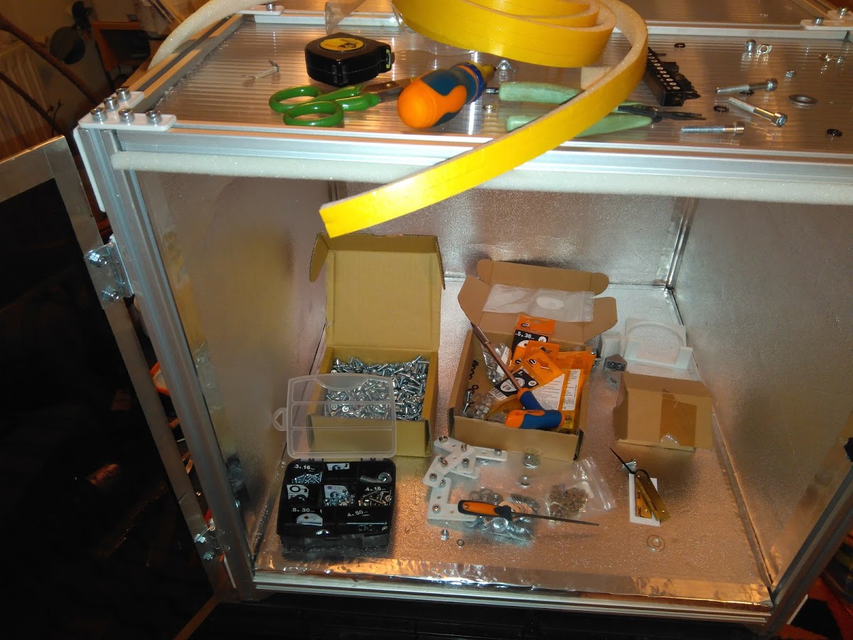
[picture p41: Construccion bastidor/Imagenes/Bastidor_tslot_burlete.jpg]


**La puerta es de metacrilato de 4mm** en este caso al no ser muy grande la hacemos de esta manera. **Tiene  el lado interior recubierto de film semireflectante** para que la luz rebote en el interior y se aproveche mejor, asi como para evitar el deslumbramiento, ya que la luz que tendremos en el interior es muy brillante. Las aristas estan recubiertas de cinta de aluminio. Unos agujeros pasantes nos permiten fijarla con bisagras, poner el mango y unos imanes para el cierre, quedando de esta forma completamente funcional. 

Hablaremos mas adelante de la electrónica que debemos tener, tanto dentro como fuera, pero en la foto que sigue vemos el aspecto de la máquina una vez terminada y conectada. El color morado tirando a rosa es hipnotizante:

MVP de aluminio

También hablaremos en otro momento del software, su instalación y características, en la foto que sigue lo vemos ya registrando datos:

MVP de aluminio

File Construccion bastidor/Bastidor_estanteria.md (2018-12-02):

# Bastidor a partir de estanterías metálicas

En este caso construimos un **bastidor con una estantería metálica** de venta en cualquier ferretería o centro de bricolaje y la forramos con paneles que pasamos a describir.

La estantería de **este caso es de 120cm de ancho y 50cm de fondo**. el coste fue de unos 60euros. Se puede partir en dos módulos, quedando uno diáfano (el de la dcha) y otro con una división interior (el de la izda.) De este modo tenemos un ancho total de 220cm y una altura de 90cm. En la foto lo podemos ver antes de panelar:

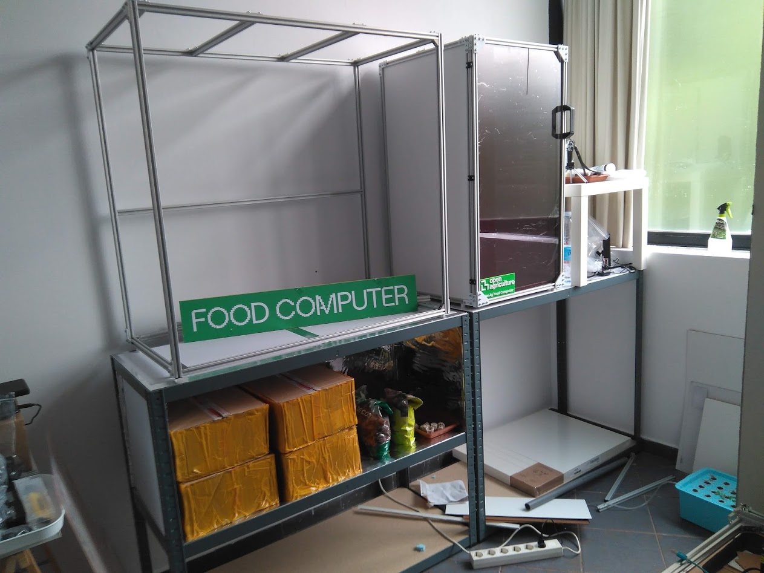
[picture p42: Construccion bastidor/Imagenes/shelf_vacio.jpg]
shelf_vacio


Los **paneles tanto laterales como traseros** los hacemos con **poliestireno extruido** (no expandido, este es el porexpan o corcho blanco, mucho mas frágil). Un panel de este tipo cuesta unos 4-5eur (120x60cm). Es fácil de cortar con cutter a la medida que necesitamos. En la foto vemos el trasero colocado y el lateral derecho a punto de colocar. entran a presión, no hace falta que esten pegados.

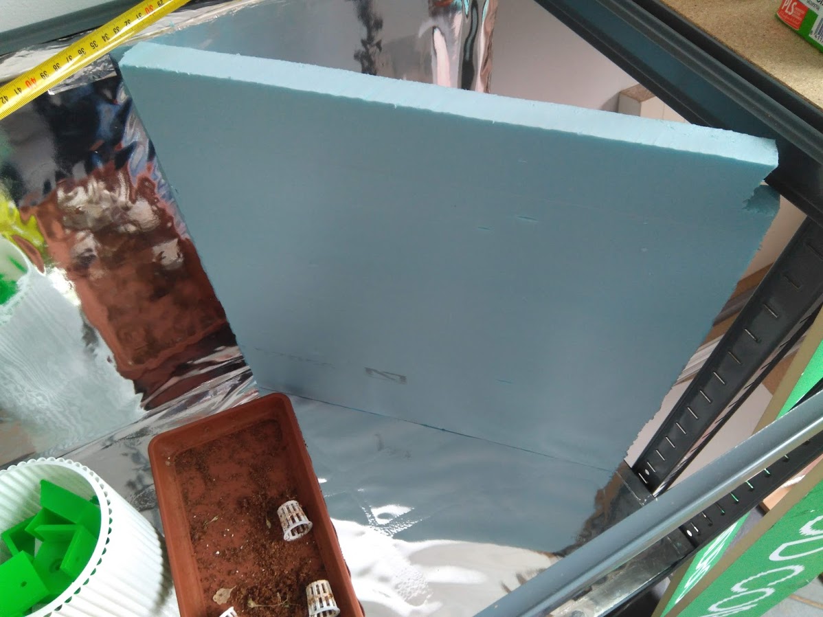
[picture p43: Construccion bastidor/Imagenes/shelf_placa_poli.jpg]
shelf_placa_poli


Cada una de estas placas la forramos internamente con plástico aluminizado y externamente con film blanco adhesivo. En el perímetro pegamos cinta de aluminio. En la foto vemos el mismo panel lateral ya preparado y a pounto de colocar:

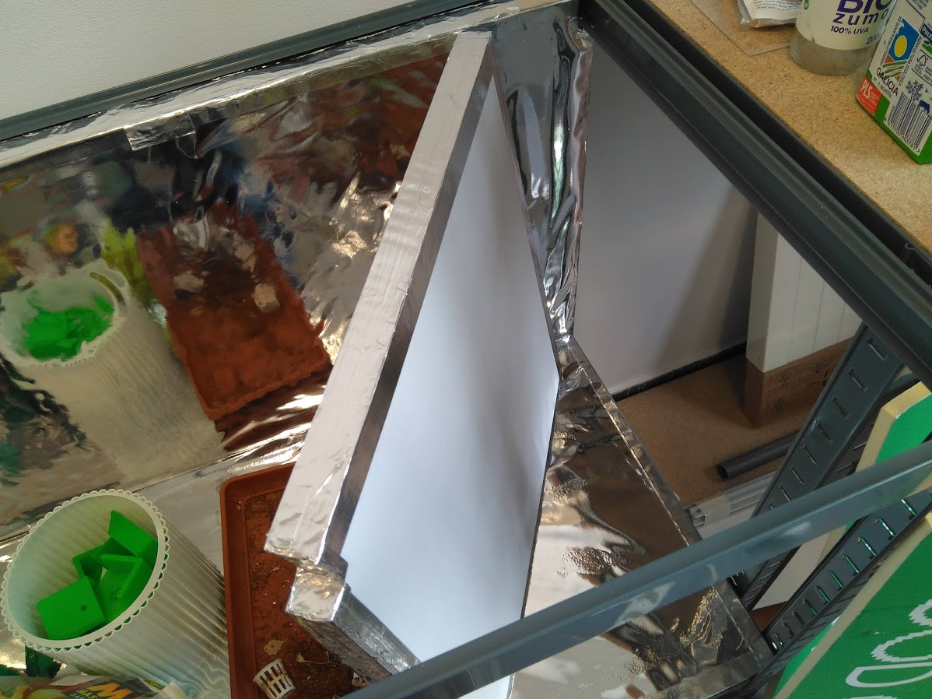
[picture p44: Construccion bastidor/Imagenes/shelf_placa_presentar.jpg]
shelf_placa_presentar


**Las planchas de madera que lleva la estantería** las forramos de plastico aluminizado en sus caras interiores. En su cara superior, la que queda a la vista, de film blanco adhesivo.

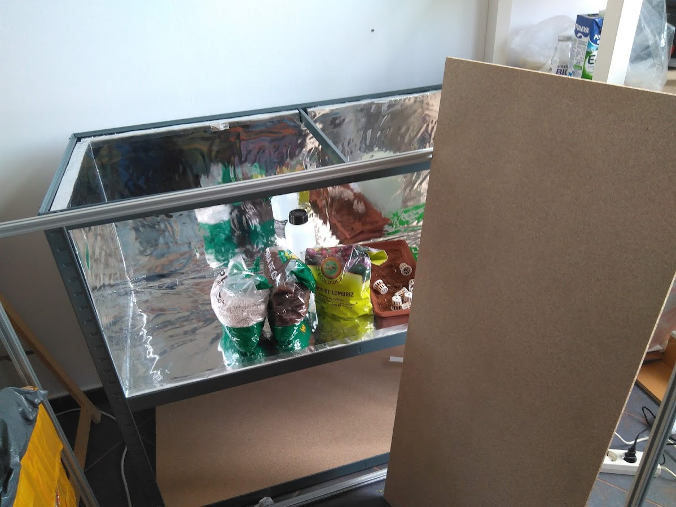
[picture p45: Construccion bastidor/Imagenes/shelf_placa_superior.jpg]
shelf_placa_superior


Una vez forrado todo el interior **colocamos las barras LED** en su parte superior. El módulo diáfano tendrás dos barras, mientras que el doble tendrá solo una en el nivel superior. El nivel inferior tendrá depósitos de líquidos ya que en este módulo emplearemos la técnica ebb&flow de la que ya hablaremos en el apartado de cultivo. Las barras LED tienen 85W cada una. Las fijamos al panel mediante hembrillas tal y como se ve en la foto:

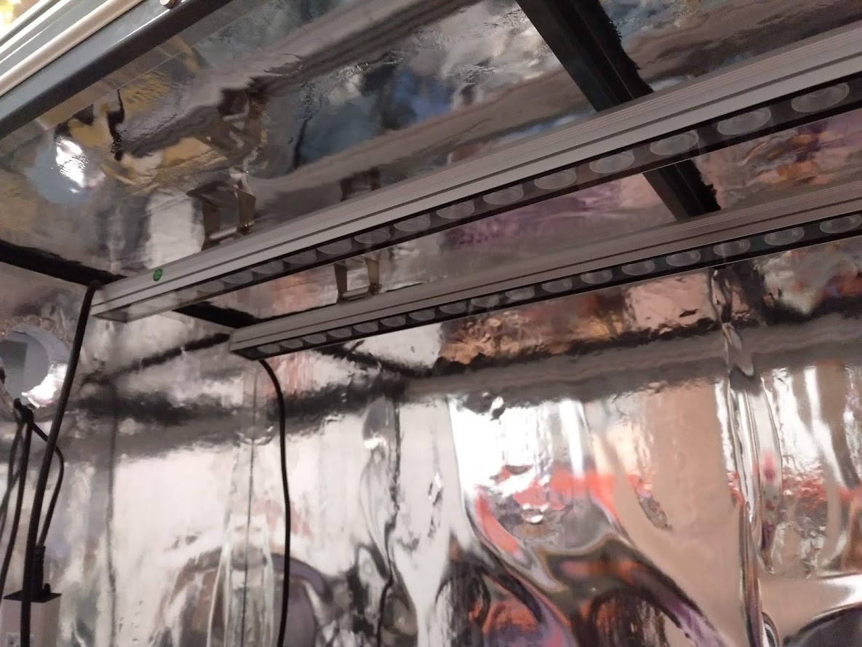
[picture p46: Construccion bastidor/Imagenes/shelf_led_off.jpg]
shelf_led_off


En estos MVPs empleremos la técnica **ebb&flow** y mas adelante **cultivo de alga spirulina** e incluso quizás un **pequeño módulo acuapónico**. Para todo ello emplearemos unas cajas de uso alimentario que se pueden apilar. Hay dos niveles, el superior contendrá el sustrato y el inferior el líquido para el riego, que se movera de forma periódica con una bomba. En la foto vemos estas cajas  en su proceso de colocación. Falta la fontanería necesaria para que el bombeo funcione. 

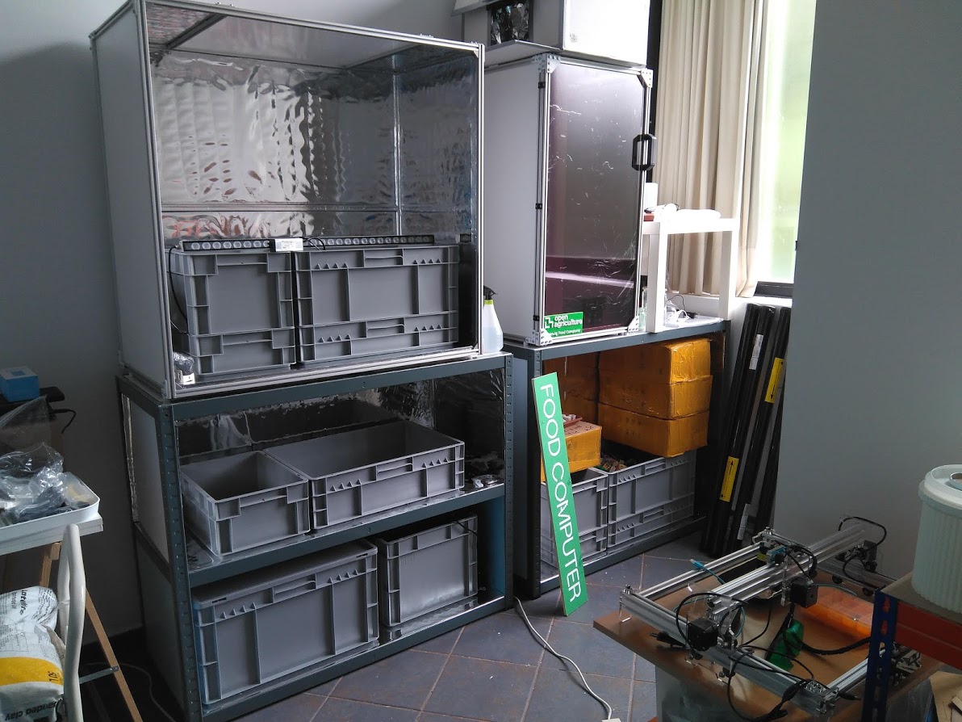
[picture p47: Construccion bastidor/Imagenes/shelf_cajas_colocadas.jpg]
shelf_cajas_colocadas


Y por último una prueba de encendido con uno de los módulos. **Las puertas son grandes** y por tanto también **de policarbonato alveolado**. Forrado internamente de film semireflectante y con perímetros de cinta de carrocero. En un módulo a rojo y en el otro en azul.

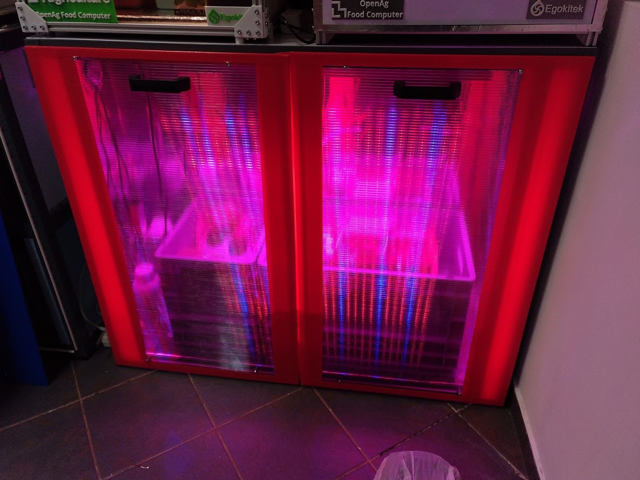
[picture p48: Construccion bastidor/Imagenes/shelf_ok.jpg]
shelf_ok


En otros apartados del proyecto se explican el resto de detalles.

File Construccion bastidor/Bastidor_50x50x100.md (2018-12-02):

# Bastidor con perfiles de aluminio 50x50x100cm

Se trata de construir el bastidor con perfiles de aluminio **TSLOT** de 20x20mm y ranura de 6 mm. Se pueden comprar con  la longitud cortada a la medida que queramos, aunque es mejor usar valores mas o menos estandar. Estos perfiles son relativamente baratos, asi que **el coste total del bastidor es bajo, al tiempo que conseguimos una estructura ligera y rígida, con un aspecto muy profesional**.

Veamos en esta primera foto el aspecto que tiene el bastidor ya montado:

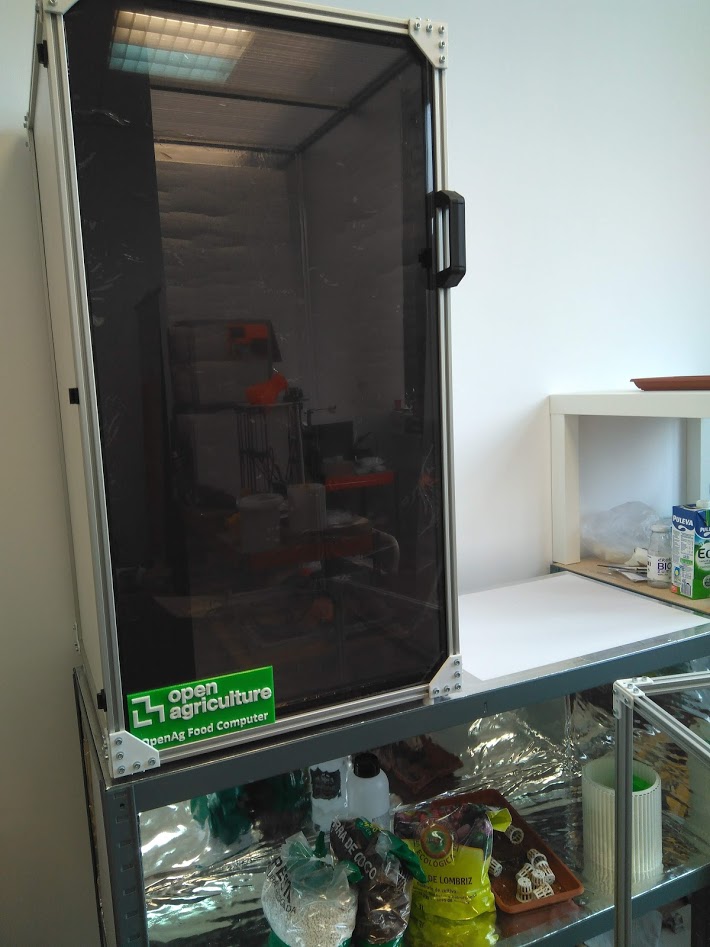
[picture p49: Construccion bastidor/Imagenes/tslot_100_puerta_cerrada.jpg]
Puerta_cerrada


Con la apertura de la puerta vemos su interior. El sistema de montaje es como el del bastidor 50x50x50cm que ya hemos visto.

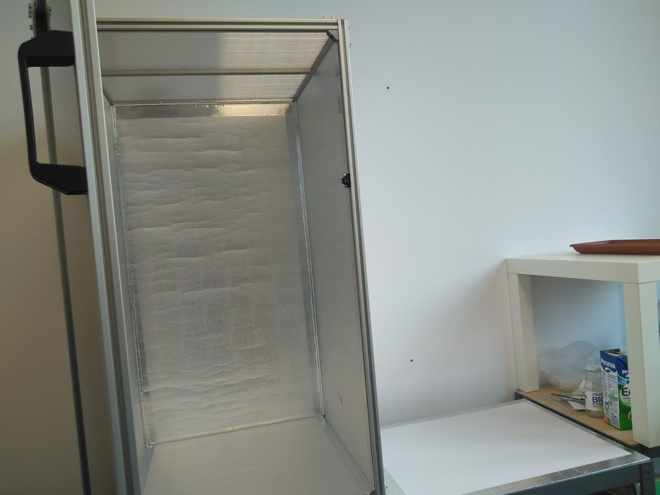
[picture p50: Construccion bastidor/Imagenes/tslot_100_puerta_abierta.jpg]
Puerta_abierta


La iluminación en el interior es diferente. Para este caso hemos empleado el sistema de diseño del **Food Computer MVP** original, que emplea 4 bombillas LED de 16W. 

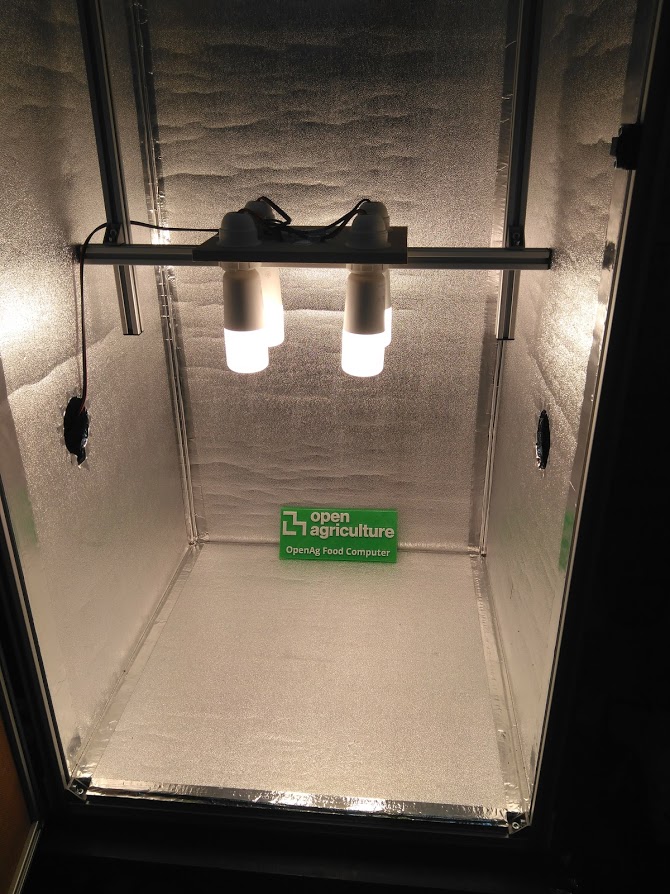
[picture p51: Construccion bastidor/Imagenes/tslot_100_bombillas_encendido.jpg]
Encendido


Aqui vemos el sistema desde abajo, está fijado a una barra que se puede levantar para estar a la distancia adecuada de las plantas:

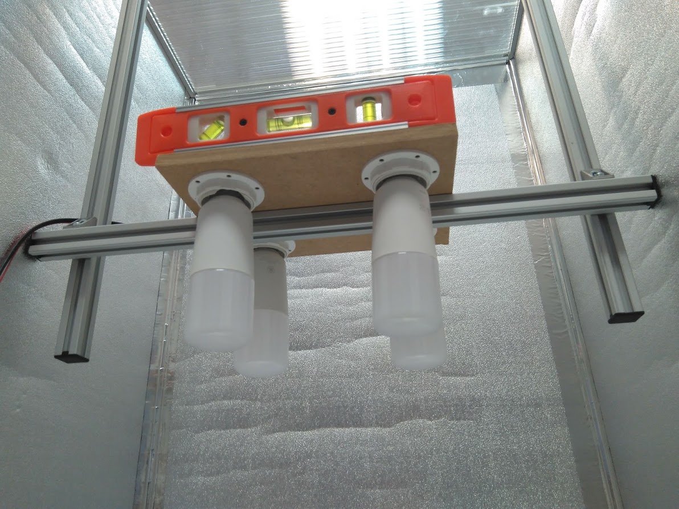
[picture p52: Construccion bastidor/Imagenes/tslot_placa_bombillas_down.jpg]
Bombillas


Para hacerlo he empleado un trozo de mandera DM de 1cm, al que he hecho 4 agujeros para encajar el soporte de la bombilla. Estas dan una luz blanca de unos 3000K y 1500lm cada una.

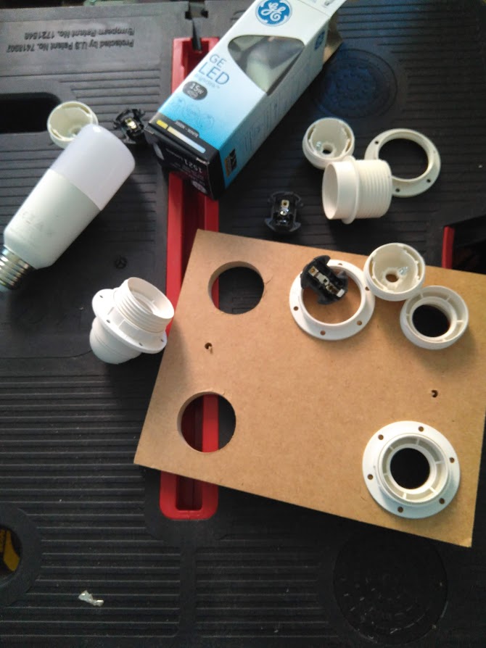
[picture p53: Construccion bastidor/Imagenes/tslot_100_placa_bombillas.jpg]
Montaje_bombillas


Conectamos el cableado y lo fijamos a la placa en la parte superior, quedando de esta manera. Hay que ser muy cuidadoso en todo este proceso ya que estaremos trabajando con tensiones de 220AC.

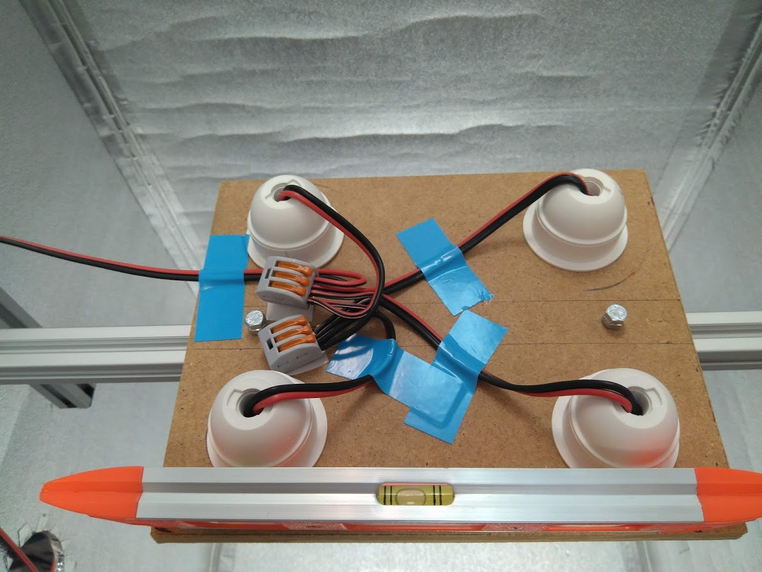
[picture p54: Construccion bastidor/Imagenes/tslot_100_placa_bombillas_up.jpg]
Conexiones_bombillas


El resto de detalles constructivos son como el del FC 50x50x50 que ya se ha explicado.

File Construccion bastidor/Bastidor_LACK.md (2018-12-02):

# Bastidor LACK

**A continuación mostraré como montar un bastidor de 50x50x50cm** con un kit de mesa de la casa IKEA,, llamado **LACK**. Tiene la ventaja de ser muy barato, unos 10euros. 

En la comunidad de impresión 3D surgió la idea de utilizar esta mesa para recubrir las impresoras. Si se panelan permiten crear un espacio cerrado de temperatura estable, que permite imprimir ciertos materiales difíciles como el ABS. Para hacerlo posible se diseñaron unas piezas que permiten que todo el conjunto encaje correctamente y cumpla esa función. He incluido esas piezas en el proyecto (en la carpeta STL) y he añadido una subcarpeta adicional con mis propios diseños para adaptar el diseño y asi sirve como Food Computer.

Aquí vemos el inicio del ensamblaje:

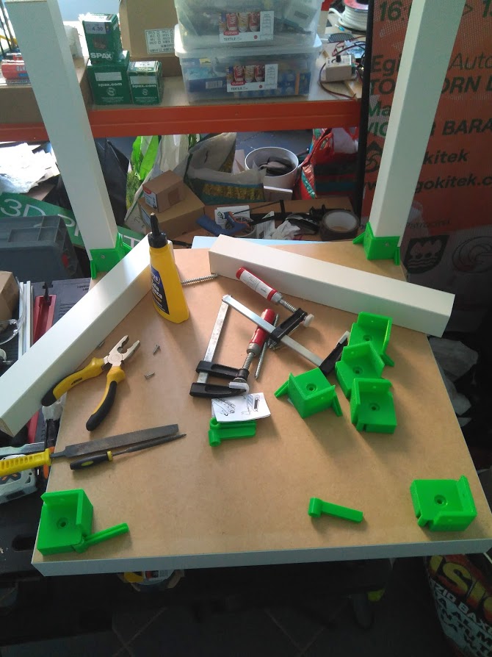
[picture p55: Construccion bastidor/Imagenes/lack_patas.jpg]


La mesa se compone de las 4 patas y el tablero. Las unimos entre si con una pieza impresa entre ambas, luego veremos para que sirve. Empleamos cola blanca y tornillos de 4x40. Las patas se pueden fijar lateralmente a la pieza en 3D en los dos lados interiores. Para esta unión lateral se usan tornillos mas pequeños de 3,5x16. Vemos todo esto en la foto.

Una vez montadas las patas y antes de fijarles la base colocamos los paneles laterales. Deben tener un espesor de 2,5mm aproximadamente para que entren en unos insertos que tienen las piezas en 3D. En mi caso he usado para el panel trasero una placa de madera DM plastificada en blanco (e internamente cubierta de aluminio). Esta placa tiene 3mm y la he tenido que rebajar un poco para que entre en los insertos.

Las placas laterales son de plástico de 2,5mm asi que entran correctamente. Ambas están recubiertas internamente de film semireflectante para evitar la pérdida de la luz interior y reducir el deslumbramiento cuando miramos al equipo. Deben tener dos agujeros circulares de unos 8cm de diámetro, que servirán para la entrada y salida de aire. Uno de ellos debe estar alineado con la placa de control que estára en el exterior. En la foto que sigue vemos el aspecto que tiene:

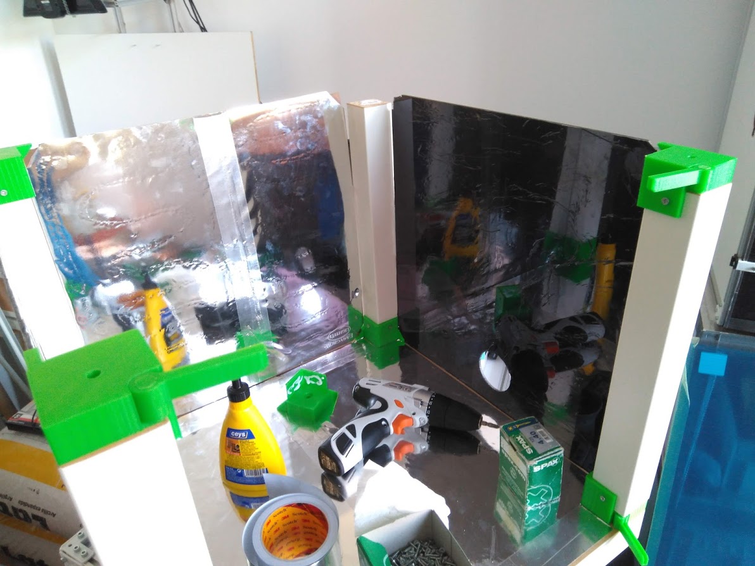
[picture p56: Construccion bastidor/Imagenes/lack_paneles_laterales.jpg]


Nos queda la puerta. También es de plástico y 2,5mm. Internamente forrada de film semireflectante y aluminio como vemos en la foto:

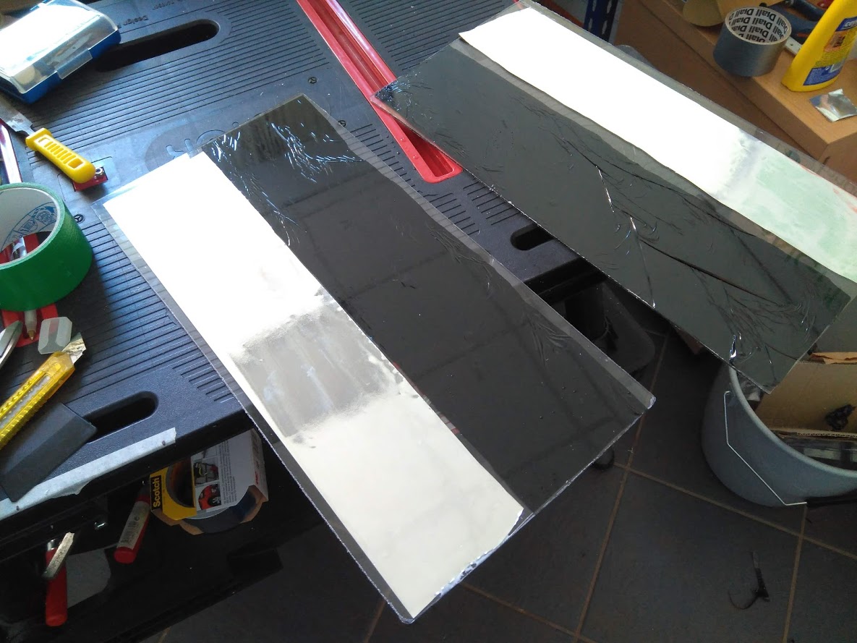
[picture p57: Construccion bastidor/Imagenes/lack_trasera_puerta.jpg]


En la parte frontal lleva una franja de film blanco. Todas las aristas están forradas con cinta de carrocero verde. En la foto vemos el aspecto que va a tener:

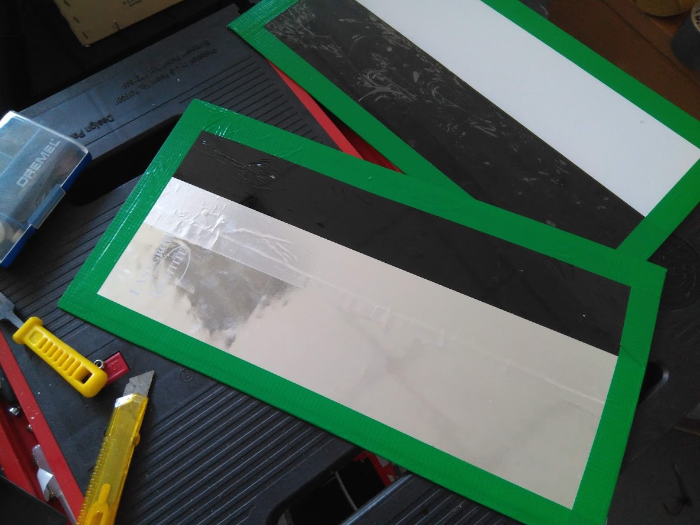
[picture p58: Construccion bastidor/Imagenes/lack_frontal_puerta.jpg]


En este caso vemos que se forman burbujas al colocar el fim semireflectante ya que es muy fino, no lo recomiendo. En el futuro prefiero comprar si es posible   el plástico ya tintado a un proveedor especializado.

La base del bastidor será una plancha de madera DM de 1cm y aproximadamente 50x50cm . La forraremos con film blanco y la fijaremos al resto del chasis con cola blanca y tornillo de 4x40 . Este es el aspecto que tiene:

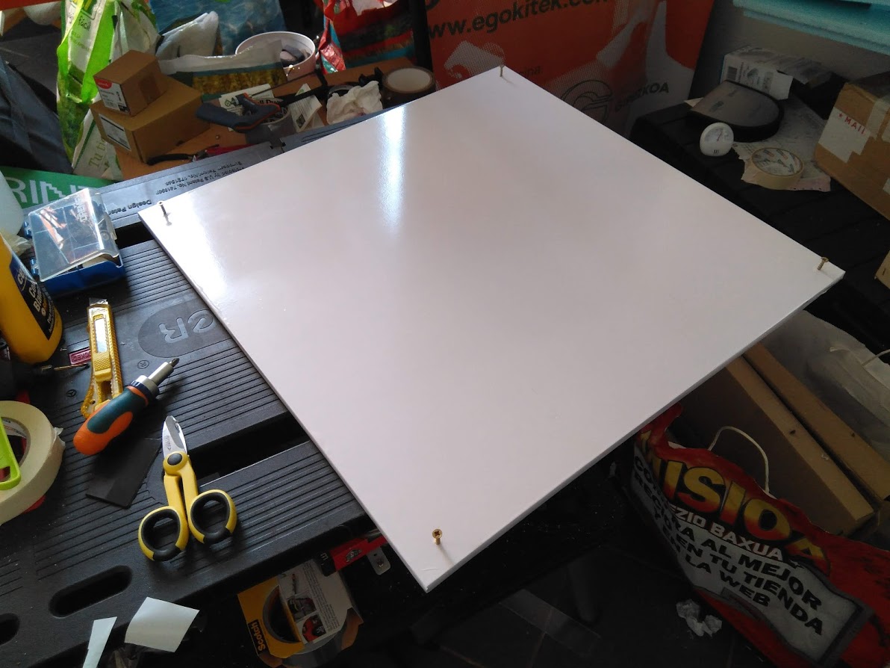
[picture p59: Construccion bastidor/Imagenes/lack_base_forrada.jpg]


El aspecto del bastidor terminado es este. La puerta inserta en las ranuras de las "bisagras" que van insertas en las piezas en 3D (estas piezas van tanto arriba como abajo para sujetar la puerta desde ambos puntos). En las juntas de unión de los paneles podemos aplicar silicona blanca  para que el sellado sea bueno. También se puede poner un burlete en la puerta.

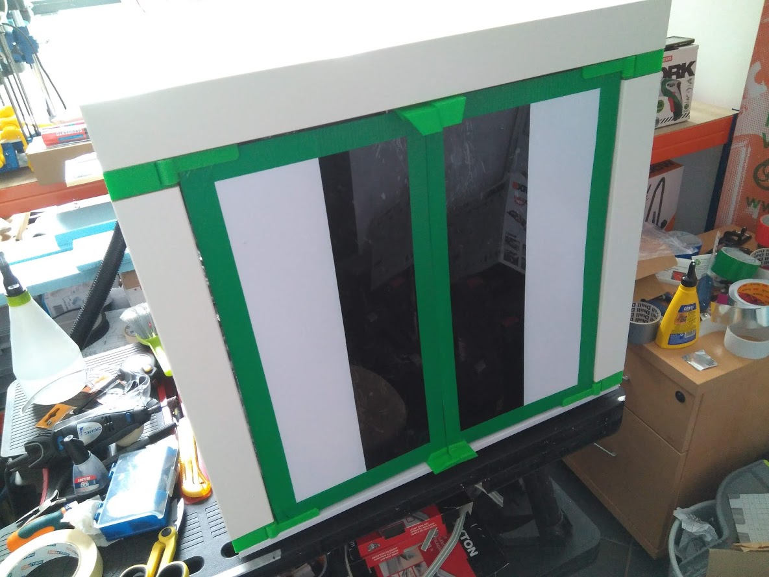
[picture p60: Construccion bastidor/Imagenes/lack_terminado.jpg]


Este bastidor es de 50x50x50 que es un tamaño bastante apto, pero podemos hacer un bastidor de 50x50x100cm para cultivos mas grandes si unimos dos mesas LACK. Una abajo y dada la vuelta y otra arriba. O sea, la plancha de la mesa hará de base en la mesa de abajo. Para unir ambas mesas en su sección central (pata con pata) he diseñado unas piezas adicionales en 3D como está que vemos aquí:

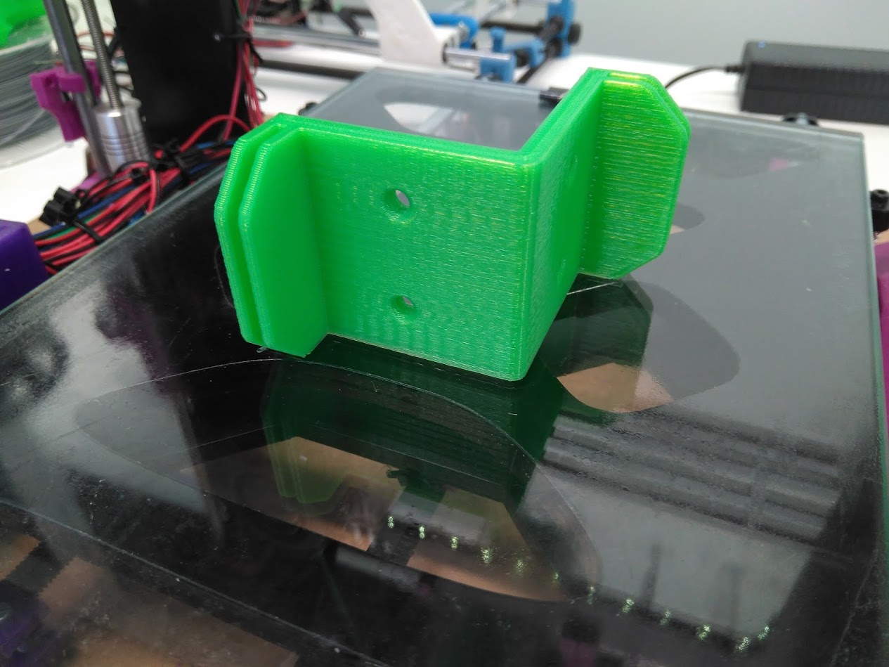
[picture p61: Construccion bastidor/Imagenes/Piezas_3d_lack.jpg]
Piezas en 3D


El panel LED en el interior lo fijamos mediante tornillo, pero debe guardar cierta distancia para permitir su refrigeración. He usado tornillos de 4x40 y unas tuercas para que hagan de separadores, como vemos en la foto. 

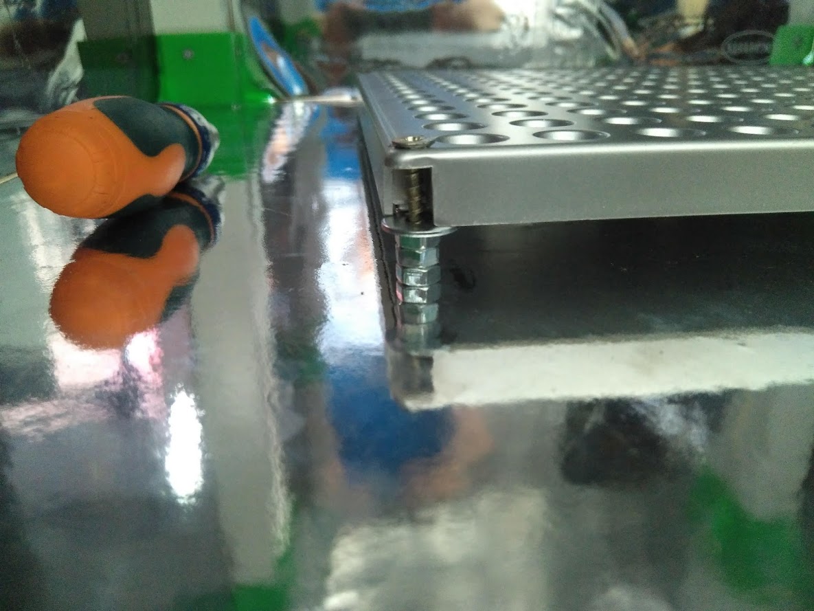
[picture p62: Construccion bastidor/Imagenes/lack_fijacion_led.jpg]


 Y ya está. A esto hace falta añadirle la placa de control (brain) pero eso lo vemos en otra sección.

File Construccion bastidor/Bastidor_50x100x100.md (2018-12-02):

# Bastidor con perfiles de aluminio 50x100x100cm

Se trata de construir el bastidor con perfiles de aluminio **TSLOT** de 20x20mm y ranura de 6 mm. Se pueden comprar con  la longitud cortada a la medida que queramos, aunque es mejor usar valores mas o menos estandar. Estos perfiles son relativamente baratos, asi que **el coste total del bastidor es bajo, al tiempo que conseguimos una estructura ligera y rígida, con un aspecto muy profesional**.

Veamos en esta primera foto el aspecto que tiene el bastidor ya montado y abierto. Como vemos **se emplea un material reflectante diferente**.
Es un film grueso y aluminizado, muy eficaz para cultivos de interior. Tenemos la fijación de la luz que se puede regular en altura como en los otros modelos:

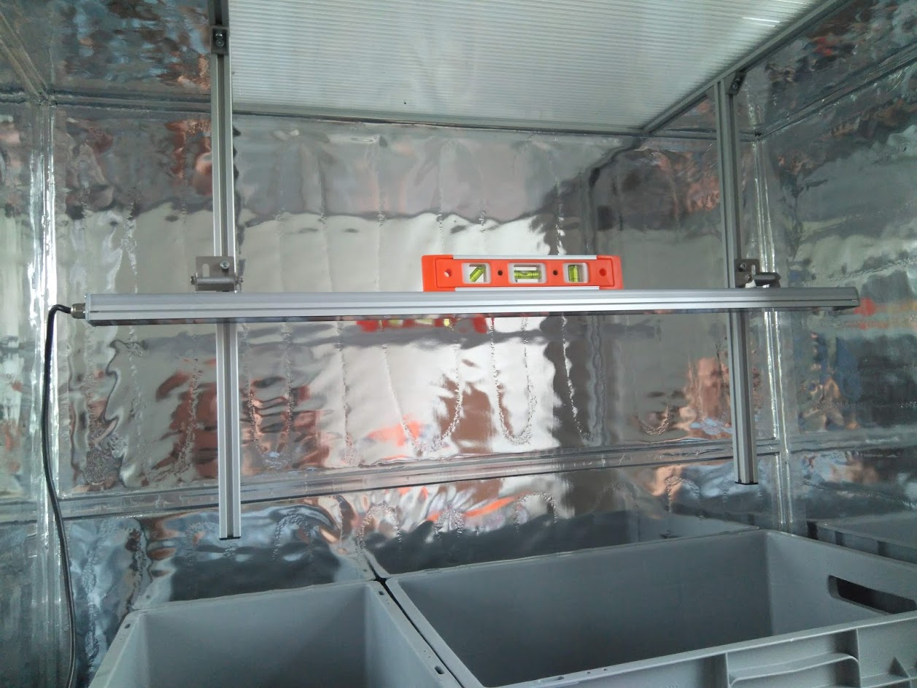
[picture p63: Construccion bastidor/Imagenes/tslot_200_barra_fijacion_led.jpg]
Interior


La barra lateral es la propia luz LED que en este caso tiene 85W. En la foto la vemos encendida:

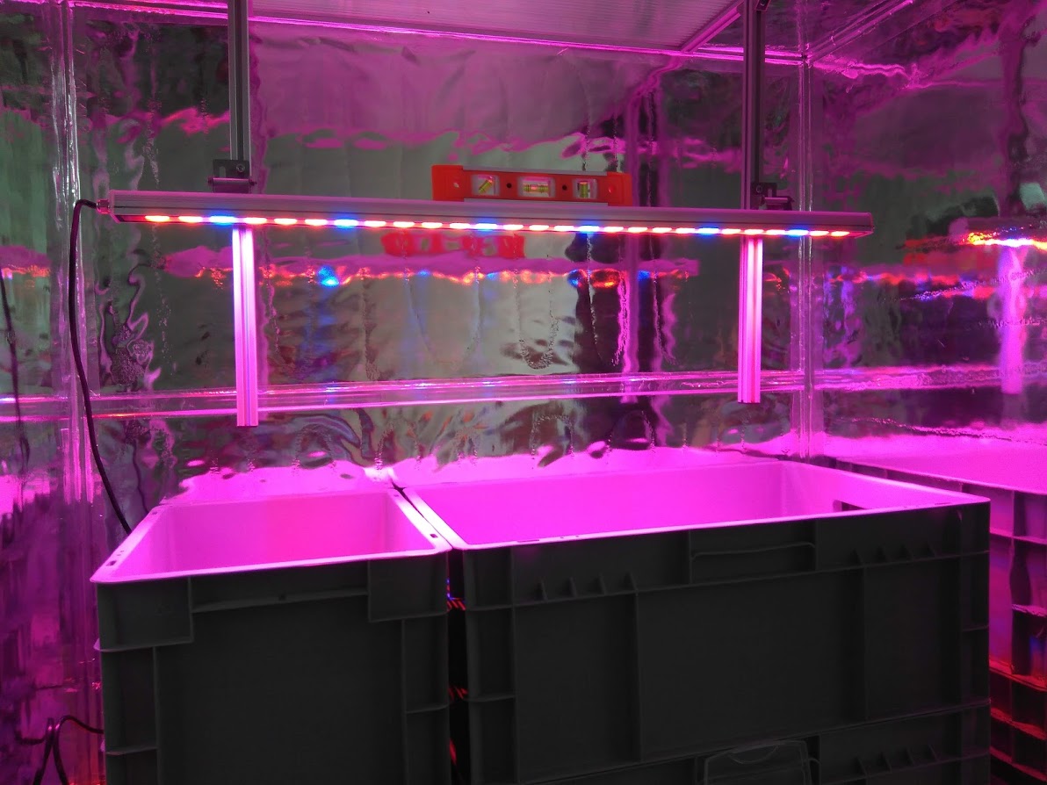
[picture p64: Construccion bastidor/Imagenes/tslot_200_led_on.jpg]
Encendido


La puertas, al ser grandes y para evitar problemas de peso, las he hecho en policarbonato alveolado. Es liviano y buen aislante térmico. Para fijarlo al chasis usamos una bisagra estandar con un acople impreso en 3D que he diseñado para este caso. Es la pieza blanca que vemos en la foto:

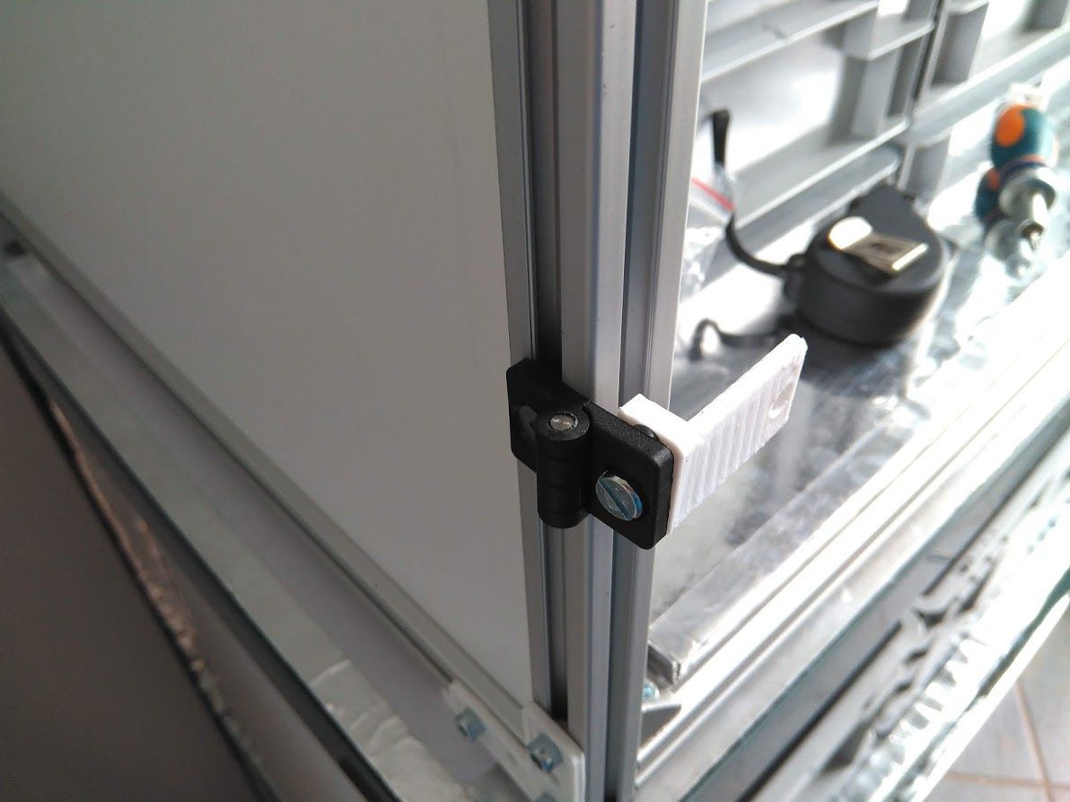
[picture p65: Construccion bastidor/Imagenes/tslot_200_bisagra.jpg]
Puerta_bisagra


Las puertas las forramos internamente con film semireflectante y el perímetro en cinta de aluminio. El resultado, una vez colocado y con la luz encendida se ve de esta manera:

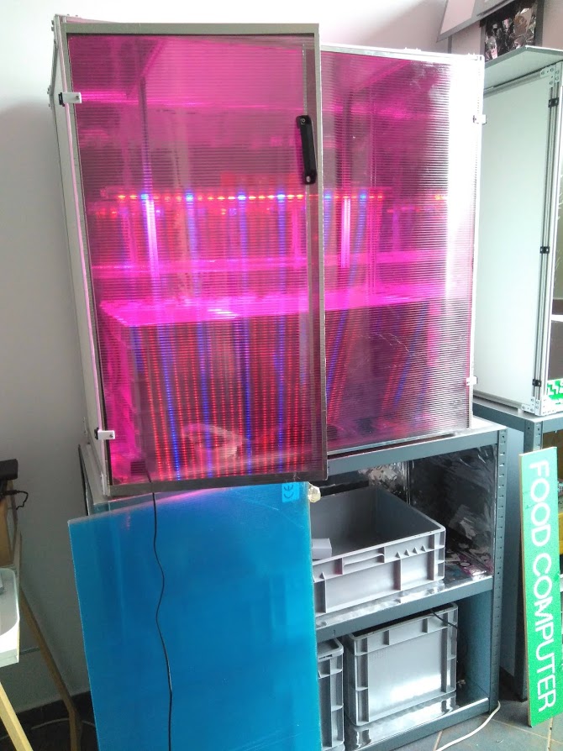
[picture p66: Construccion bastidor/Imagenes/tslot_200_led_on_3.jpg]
Terminado


El resto de detalles constructivos son como el del FC 50x50x50 que ya se ha explicado.

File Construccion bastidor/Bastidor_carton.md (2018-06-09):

# Bastidor con caja de carton

## Dimensiones de 60x40x40 cm

**Se puede hacer un bastidor de Food Computer con algo tan simple como una caja de carton**, si el objetivo es ahorrar en coste el máximo posible. Debe ser una caja lo bastante grande y bien conservada. En este ejemplo he empleado una caja de 60x40x40 cm, que externamente es blanca y resulta mas estética.

**Para reforzarla ponemos cinta americana en todas las aristas**. Esto tambien mejora su aspecto estético, hemos de ponerla con un poco de cuidado para que quede bien.

**Cortamos con un cutter un hueco tanto en la parte superior como uno mas pequeño en el frontal**. En ambos ponemos un trozo de plástico que podemos reusar de algun embalaje. Si lo hemos de comprar hablamos de un plástico acrílico o metacrilato, de espesor fino, 1-2mm. Los fijamos mediante cinta americana.

**El interior de la caja debe forrarse con material reflectante**. Podemos usar **papel de aluminio** pero se rompe con facilidad. Es mejor usar una toalla de supervivencia, son muy baratas (unos 3eur), están hechas de un material llamado **Mylar**, es un plástico muy fino y aluminizado. Lo pegamos mediante cola blanca o cinta de doble cara. Es un material un poco dificil de manipular y es casi inevitable que aparezcan pliegues, pero es muy reflectante y también barato.

Los dos trozos de cartón que hemos cortado previamente los forramos también de mylar y los fijamos a al caja, usando cinta americana a modo de bisagra.

**Para abrir o cerrar las dos compuertas** que acabamos de describir usamos un trozo de **velcro**. En la foto que sigue a continuación vemos la caja terminada:

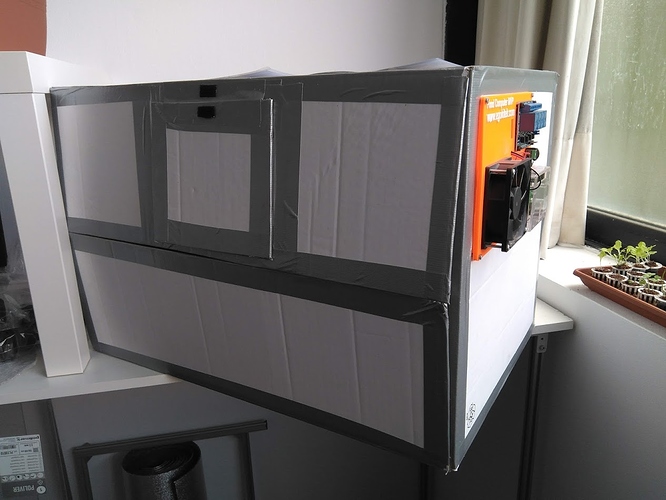
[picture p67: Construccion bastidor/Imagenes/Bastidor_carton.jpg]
MVP de carton


Los dos pequeños cuadros negros en el frontal son las piezas de velcro, sirven para mantener abierta la ventana frontal cuando la levantamos. En la siguiente foto lo podemos ver:

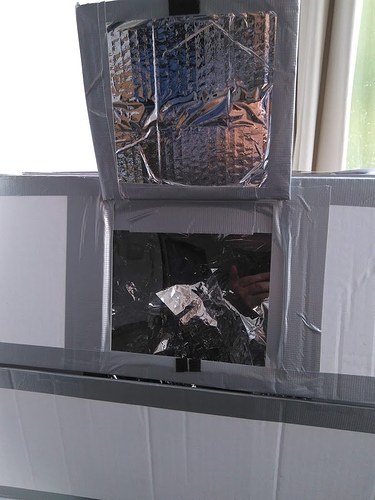
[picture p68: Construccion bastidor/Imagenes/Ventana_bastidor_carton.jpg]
Ventana frontal


**La tarjeta de control** la podemos fijar atrás o en un lateral, en este caso se ha fijado en el lateral derecho. No pesa mucho y no afecta a la integridad de la caja. La tarjeta que se muestra era una primera prueba de concepto y está en evolución, no es el aspecto que tendrá finalmente.

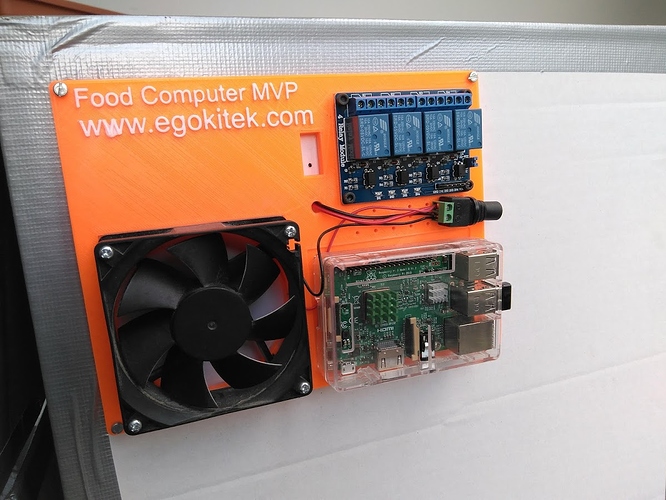
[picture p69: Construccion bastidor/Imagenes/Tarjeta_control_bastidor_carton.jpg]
Tarjeta de control


El inconveniente de usar un bastidor de este tipo es que **es díficil de fijar la luz en el interior**, además hemos de tener en cuenta que disipa una cierta cantidad de calor. Estoy probando diferentes soluciones y para este tipo de bastidor no he encontrado todavía la mas satisfactoria. Cuando lo haya testado actualizaré esta información.

**La caja terminada, con su ordenador Raspberry Pi conectado a teclado y monitor externo, y con la luz encendida tiene este aspecto**. Esta foto fue tomada en la Bilbao Maker Faire de Diciembre de 2017, donde expuse este bastidor como prueba de concepto.

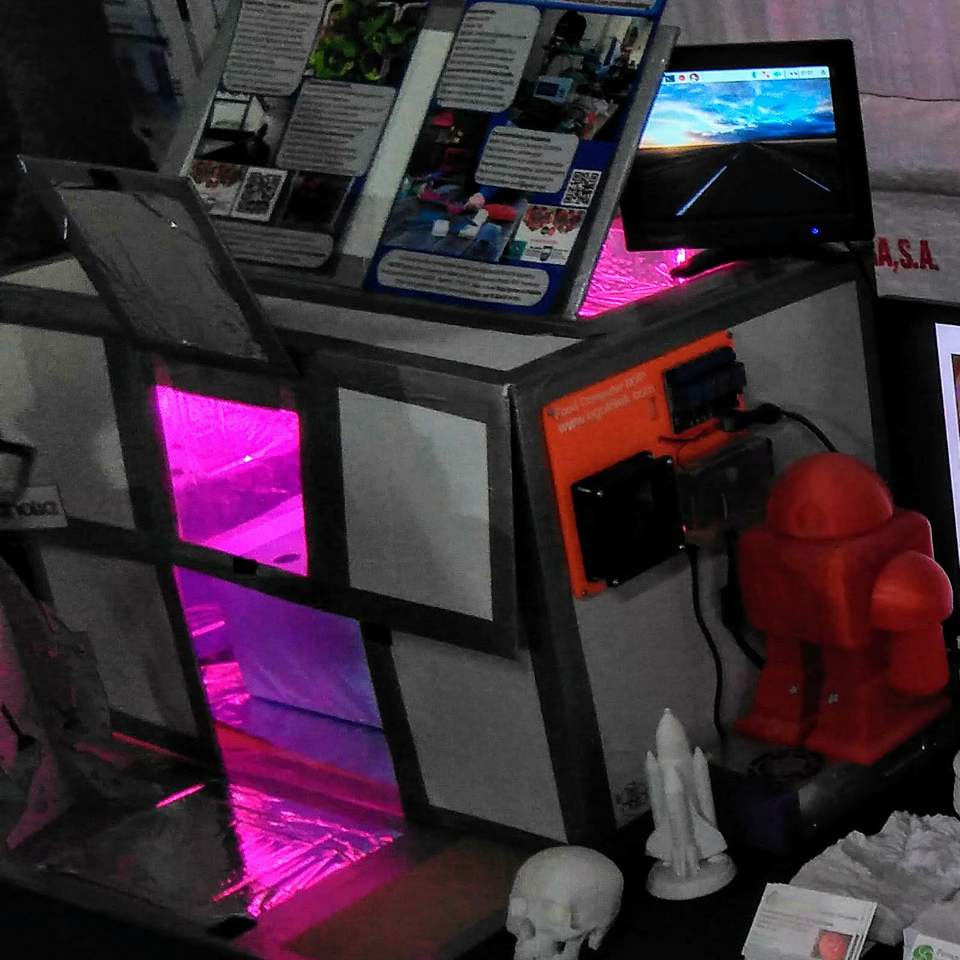
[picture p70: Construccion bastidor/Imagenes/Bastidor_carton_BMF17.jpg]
En la Bilbao MF17


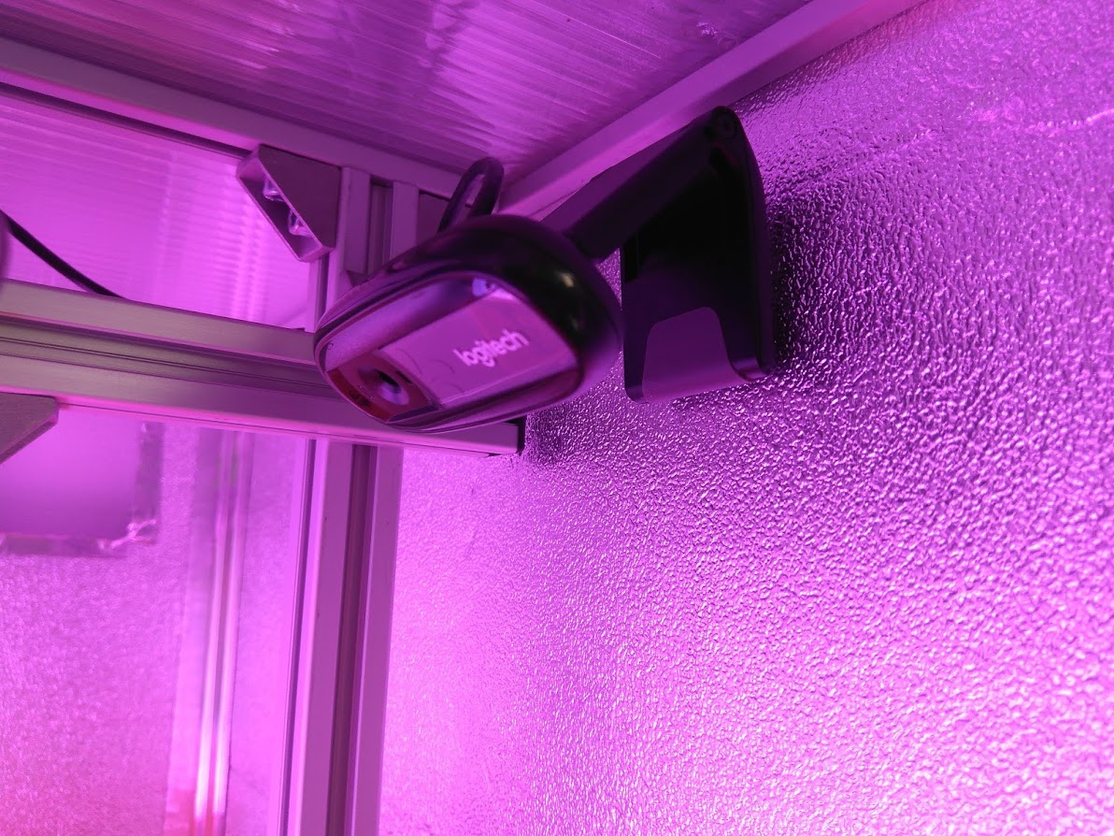
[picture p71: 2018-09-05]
Construccion bastidor/Imagenes/Bastidor_tslot_fijacion_webcam.jpg

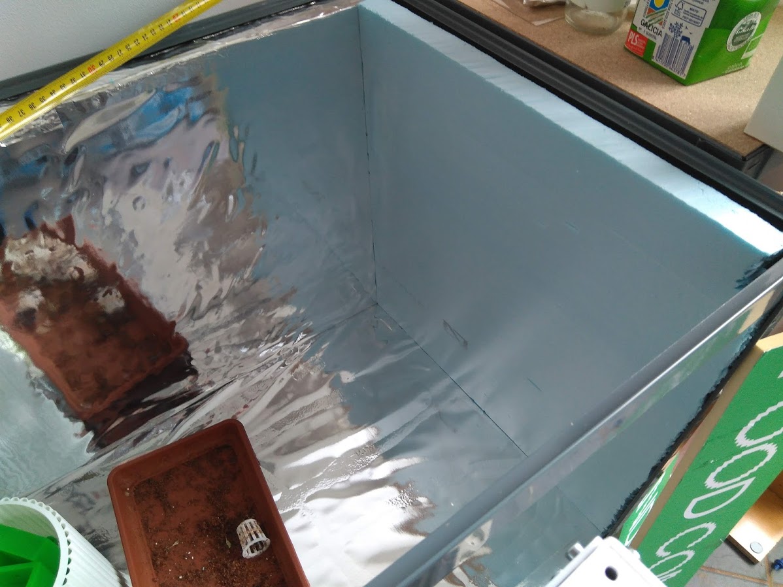
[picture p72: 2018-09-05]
Construccion bastidor/Imagenes/shelf_placa_poli_2.jpg

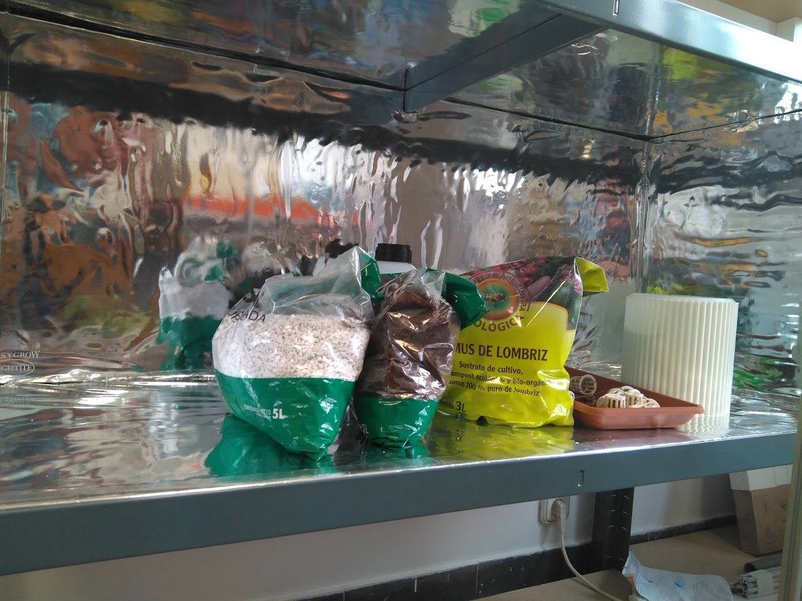
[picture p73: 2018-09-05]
Construccion bastidor/Imagenes/shelf_interior_aluminio.jpg

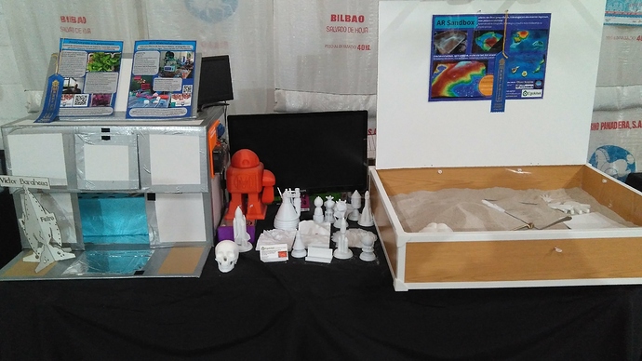
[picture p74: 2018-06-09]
Construccion bastidor/Imagenes/Bastidor_carton_BlueRibbon.jpg

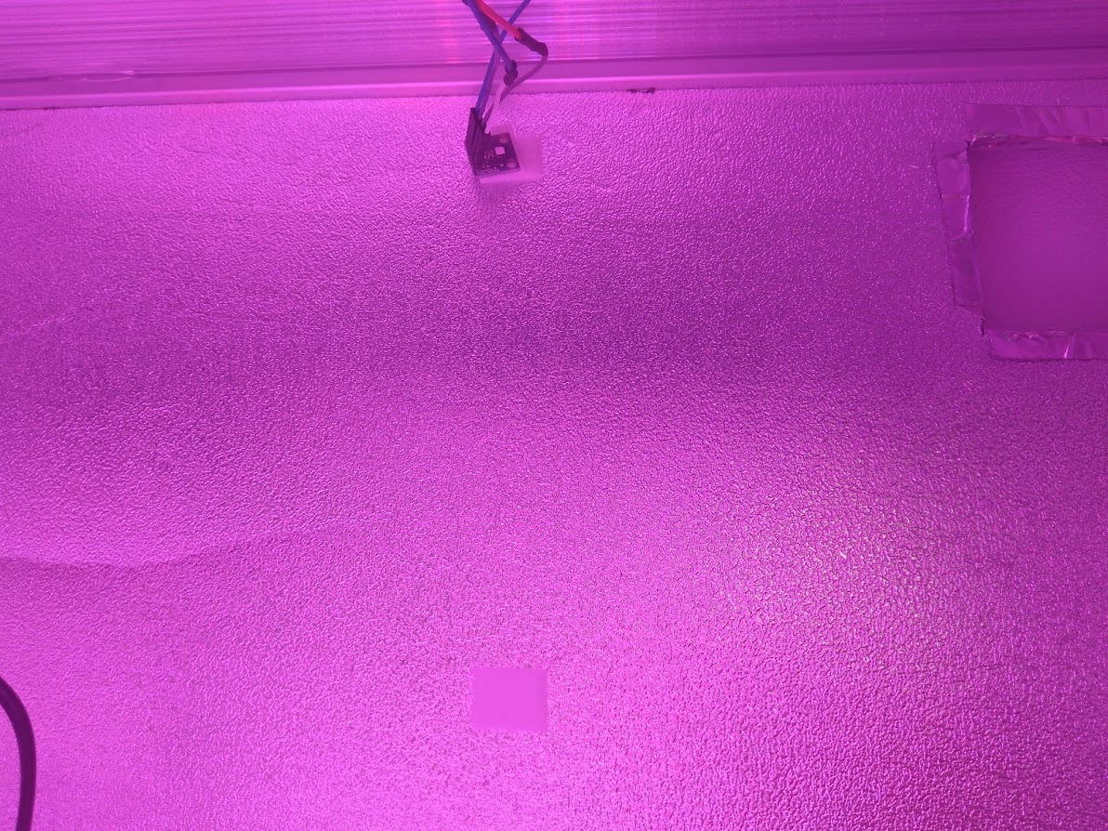
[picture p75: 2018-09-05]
Construccion bastidor/Imagenes/Bastidor_tslot_fijacion_sensor.jpg

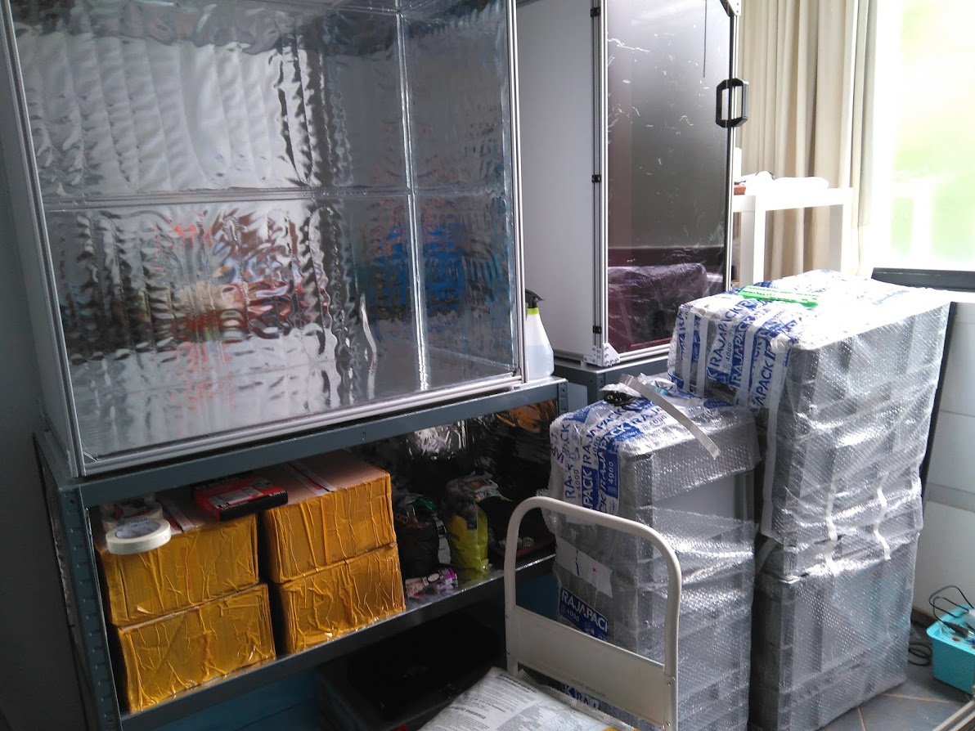
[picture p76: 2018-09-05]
Construccion bastidor/Imagenes/shelf_cajas.jpg

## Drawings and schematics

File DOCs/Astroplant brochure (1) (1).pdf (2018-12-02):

## team + advisors

## About Border Labs

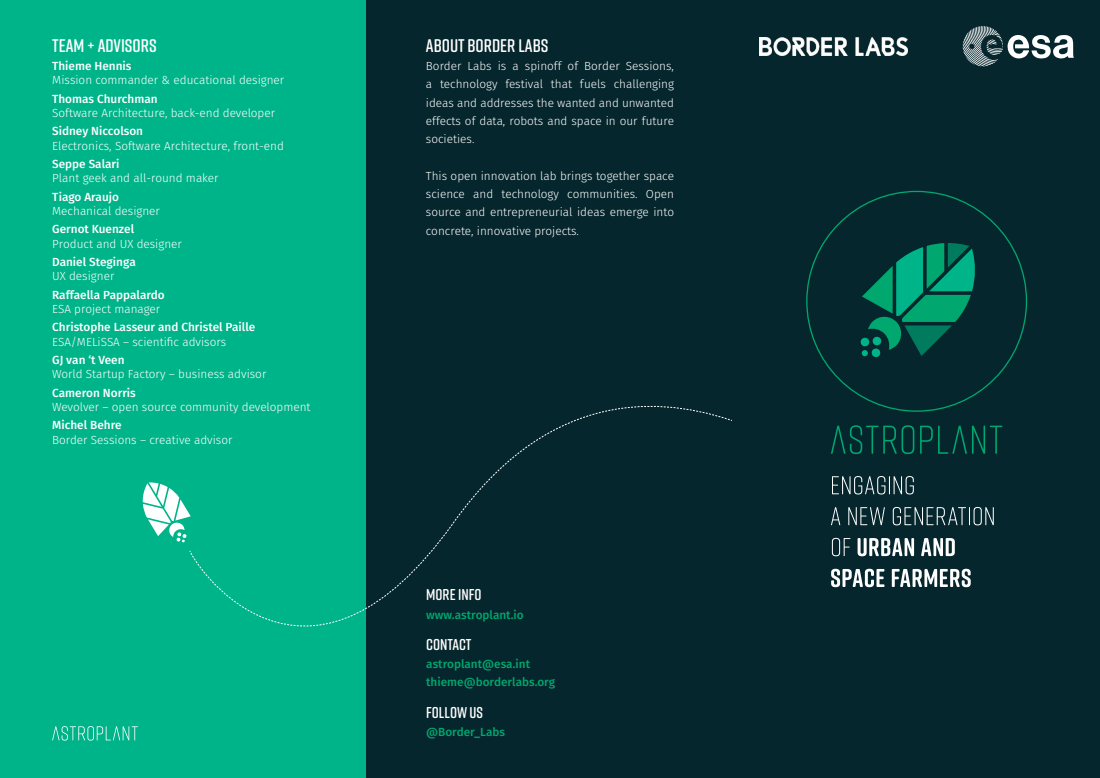
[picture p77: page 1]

Thieme Hennis
Mission commander & educational designer
Thomas Churchman
Software Architecture, back-end developer
Sidney Niccolson
Electronics, Software Architecture, front-end
Seppe Salari
Plant geek and all-round maker
Tiago Araujo
Mechanical designer
Gernot Kuenzel
Product and UX designer
Daniel Steginga
UX designer
Raffaella Pappalardo
ESA project manager
Christophe Lasseur and Christel Paille
ESA/MELiSSA – scientific advisors
GJ van ‘t Veen
World Startup Factory – business advisor
Cameron Norris
Wevolver – open source community development
Michel Behre
Border Sessions – creative advisor

Border Labs is a spinoff of Border Sessions,
a technology festival that fuels challenging
ideas and addresses the wanted and unwanted
effects of data, robots and space in our future
societies.

This open innovation lab brings together space
science and technology communities. Open
source and entrepreneurial ideas emerge into
concrete, innovative projects.

MORE INFO
www.astroplant.io
CONTACT
astroplant@esa.int
thieme@borderlabs.org
FOLLOW US
@Border_Labs

## WHAT IS ASTROPLANT?

AstroPlant is a citizen science kit to educate the next generation of urban and space farmers. It is:
- An open source plant lab
- An educational programme
- An interactive interface

AstroPlant integrates plant science, electronics and space. The kit is provided with an application showing all relevant data. These data are used by the ESA’s MELiSSA consortium to validate plant models and help improve regenerative life-support systems for astronauts.

- Human inputs: number of leaves and nodes, size, weight, pH, fruits
- Sensor data: air and water temperature, CO2 levels, humidity, electrical conductivity

AstroPlant is an open platform: anyone can customise the instrument, add new sensors and tailor it to specific plants and contexts. It enables understanding, interaction, and creativity.

## Next steps

AstroPlant has grown into a dedicated community of enthusiasts and volunteers. The core team consists of engineers, plant scientists, urban farmers, designers, and entrepreneurs.

AstroPlant is part of an ongoing educational project in Belgium, and is being tested by various makerspaces and scientists in Europe. All its designs are open source and available online.

In 2018 AstroPlant will be launched on Kickstarter to raise funds for the manufacturing and distribution of over 1000 kits across the world.

## Your involvement

We are actively looking for partners to further sponsor, develop and test the AstroPlant technology stack, mobile app, and educational programme.

By becoming a supporter of the AstroPlant mission, you will:

- Connect your brand with the AstroPlant mission
- Connect with the AstroPlant team and a wider network of talented professionals in the urban farming, space, educational and technology industry
- Participate in an open source project
- Get first-hand access to scientific data on plant characterisation

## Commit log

2018-06-09 Construccion de bastidor
2018-06-09 Caja de carton
2018-06-15 Añadir menus LEDs etc
2018-06-15 Update LED
2018-09-05 Mogollon de fotos nuevas
    [4xDampers.stl, 80mm_honeycomb_full_fan_cover.stl, Escuadra exterior.stl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]
2019-07-18 Actualizacion BOM
    [BOM.xlsx]
